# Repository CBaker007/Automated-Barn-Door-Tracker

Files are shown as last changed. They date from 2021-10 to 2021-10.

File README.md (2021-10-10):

# Automated-Barn-Door-Tracker

Astrophotography typically starts with a mount or tracker that can counteract the Earth's rotation to allow long exposure photography. The price for an entry level, commercial tracker capable of holding a DSLR camera can be $350+ USD. DIY trackers (typically called Barn Door Trackers) made of two pieces of wood, a bolt, and hand power to rotate a nut to drive the tracker have been developed. Nico Carver (YouTube Nebula Photos) has such a device with plans and how-to use it here: https://www.youtube.com/watch?v=P_qqLA0WKJg.

The goal of this project is to create a DIY Barn Door Tracker based on Nico's general design and power it with an inexpensive set of electronics (microcontroller, stepper motor, and a motor controller). Additionally, use WiFi to help control the device via a web browser. The end goal would be to create reliable, wide-field DIY Automated Barn Door Tracker for under $50 USD.

Current / near future plans are:
1) Utilize dual core microprocessors to off-load all tracking functions to a dedicated core.
2) Allow for customization and user-defined settings for fine tuning the tracking rates, WiFi settings, and UI. 
3) Use an inexpensive accelerometer to further refine the speed of the motor to more precisely match the Earth's rotation (closed loop system).
4) Slightly modify the design to create a table-top version that does not require a tripod.
5) Utilize an inexpensive ESP32 camera to aid in polar alignment.

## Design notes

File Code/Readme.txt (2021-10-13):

Automated Barn Door Tracker - Compling Code Readme.txt

By default, to program an Ardunio microprocessor, you must flashed with code onto it.  Typically, to
flash the code you must either:
    A) Have the code complied by a compiler (Arduino IDE in our case) and then immediately flashed 
       onto the microprocessor by the same compiler, or 
    B) Have special code placed on the microprocessor that allows pre-compiled code to be downloaded 
       and flashed directly onto it. (Flashing pre-complied code on a blank microprocessor without
       this special code already on it, is possible but it takes a bit of effort.

This project has code built into all versions that allows this direct flashing of pre-compiled code,
called "Over the Air" (OTA) flashing via WiFi.  So once you get the first copy flashed onto the 
microprocessor, you don't have to complie and flash future versions.  Instead you can download new
pre-compiled versions from here and flash it directly from the Automated Barn Door Tracker (ABDT) 
webpage on the microprocessor.

But your new microprocessor must have an initial version of the ABDT code flashed onto it and that still
requires compiling / flashing using the Arduino IDE.

In order to compile and flash the ABDT code in the Arduino IDE, please note the following before proceeding:
    1) These directions were written based on compiling under Windows 10 using Arduino IDE (ver 1.8.15)
       running on an ExpressIF ESP32 microprocessor with WiFi capabilities.  See the code and Parts List
       for exact processor specifications.
       Newer versions and on other platforms may be possible.
    2) Download the Arduino IDE from https://www.arduino.cc/en/software and follow the installation guide
       (Windows: https://www.arduino.cc/en/Guide/Windows)
    3) In order to compile ESP32 code, you must download and install the ExpressIF board definitions.  See the
       guide below for downloading and install them in Arduino IDE.  Just follow the directions for installing from
       Board Manager and no need to follow any OS specific directions:
       https://docs.espressif.com/projects/arduino-esp32/en/latest/installing.html#before-installing
    4) You need to install the stepper library we use.  In Arduino IDE choose Sketch/Include Library/Manage 
       Libraries/Filter for "AccelStepper" and install the latest version.
    5) The sketch uses Over the Air Updates (OTA), AKA - Updating the code via WiFi.  In particular, we are
       using the AsyncElegantOTA running an AsyncWebServer for better webpage handling. These functions
       requires several prerequisite libraries be installed for the code to compile.
       a) In Arduino IDE choose Sketch/Include Library/Manage Libraries/Filter for "AsyncElegantOTA" and install 
          the latest version.
       b) Download and add these two libraries: Download the zip file (look for Code/Download ZIP) from the 
          links below. Save each ZIP file to your computer (one for each link). Then in Arduino IDE under 
          Sketch, Include Library, Add .ZIP Libary and add each one:
          ^ ESPAsyncWebServer.h: https://github.com/me-no-dev/ESPAsyncWebServer
          ^ AsyncElegantOTA.h: https://github.com/me-no-dev/AsyncTCP
     6) You must change the microprocessor we are using in the board definitions.
        In the Arduino IDE, under Tool, Board, select "NodeMCU-32S" (under ExpressIF) if using the recommended
        microprocessor from the parts list.

When you download the Automated Barn Door Tracker code, open it in Arduino IDE and it should compile.

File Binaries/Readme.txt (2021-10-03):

Readme.txt

NEVER CONNECT THE USB TO THE MICROPROCESSOR/DEV BOARD WHILE IT IS CONNECTED TO THE STEPPER MOTOR OR THE BATTERY!!!
NOT RESPONSIBLE FOR ANY DAMAGE TO YOUR USB PORT OR THE MP!!!!

This is the pre-compiled binary for the ESP32 micropocessor and pinouts as described in the sketch:

- Board Info
     + Written for the ESPRESSIF ESP32.
     + Get microprocessor / board definitions for setting up in Arduino IDE from 
       https://docs.espressif.com/projects/arduino-esp32/en/latest/installing.html#before-installing
     + ESP32-WROOM-32D Specs (Specific board datasheet for the board developed on): http://www.hiletgo.com/ProductDetail/1906566.html)
         ^ WiFi = 802.11 b/g/n; BR/EDR + Bluetooth LE v4.2
         ^ 32 GPIO; Op Temp: -40C to 85C;
         ^ 4 MB Flash; 520KB SRAM; 448KB ROM; 0KB PSRAM; 240 MHz
         ^ MP Datasheet: https://www.espressif.com/sites/default/files/documentation/esp32-wroom-32d_esp32-wroom-32u_datasheet_en.pdf
      + There are several specific Expressif ESP32 MP Chips (like ESP32-WROOM-32D) but a whole slew of development boards
        all with different pinouts and voltages.  It is very important that you adjust your particular wiring to reflect this,
        as well as setting the pin references in this file below.  The voltage of this board supports 5.0v (not 3.3v) so the battery
        battery can power the MP and Stepper Motor without a voltage regulator.  Recommended to stick with a 5.0v board where possible 
        to avoid power issues.
      + This may run on future releases for the ESP32-WROOM-32 chip (E, F, etc.) but if you have issues, should re-compile a version
        specific for your version of the chip.
        
      + This is the specific board this binary was developed and tested on though other boards with the same specs should work:
        https://www.amazon.com/gp/product/B0718T232Z/
         - HiLetgo ESP-WROOM-32 ESP32 ESP-32S Development Board 
         - 2.4GHz Dual-Mode WiFi + Bluetooth 
         - Dual Cores Microcontroller Processor 
         - Integrated with Antenna RF AMP Filter AP STA
         - For Arduino IDE

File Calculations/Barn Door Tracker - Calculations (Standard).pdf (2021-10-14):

## Barn Door Tracker – RPM Calculation (using 1/4”-20 bolt)

### 1) Earth’s Rotation

The earth takes 23 hr., 56 min, 4.09053 seconds to rotate 1 revolution or 360 degrees. We will do our calculation for how fast the tracker must move in degrees per minute (dpm) so we will convert the dpm.
Earth DPM = 360 degrees / 23 hr., 56 min, 4.09053 sec
Earth DPM = 360 degrees / (23 hr. * 60 min/hr.) + (56 min) + (4.09053 sec * 1 min/60 sec)
Earth DPM = 360 degrees / 1,380 min + 56 min + 0.0681755 min
Earth DPM = 360 degrees / 1,436.069 min
Earth DPM = 0.25068 degrees/min

### 2) Barn Door Tracker as Right Triangle

Using trigonometry, we can approximate the barn door tracker as a right triangle with a base (bottom of tracker from the center of the hinge to the center of the drive bolt), the top board (hypotenuse), and the drive bolt at a right angle to base. We know that for a 1/4”-20 bolt, it means that the bolt has 20 threads per inch. For ease of use, let’s assume we want to calculate things based on moving the bolt about 1 revolution per minute. Therefore, we can setup our right triangle values we know (in red) with the angle α = 0.25068 degrees/min x 20 min = 5.01369°. We can set the opposite side as 1” (1 inch/20 rev. * 20 rev.).

1"
(at 20 min)

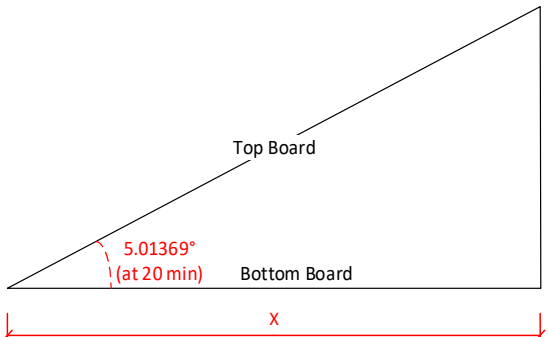
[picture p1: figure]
Top Board; Bottom Board; 5.01369° (at 20 min)

### 3) Calculate Drive Bolt Location

Using trigonometry, we can calculate the distance from the hinge to our drive bolt using: Tan(α) = Opposite/Adjacent
Adjacent * Tan(α) = Opposite
Adjacent = Opposite / Tan(α)
X = 1” / 0.087729
X = 11.40” (or 290 mm)
4) Therefore, if we place the 1/4”-20 drive bolt at 11.40” from the center of the pivot hinge, we can rotate the bolt at 1 revolution per minute to match the Earth’s rotation.
5) It is very important to understand this is an approximation. The right triangle is just an approximation for the angular movement of the Earth’s rotation. As the triangle grows (longer we turn the bolt) the more it will be off. There is very little error for runs of 20 to 25 minutes.

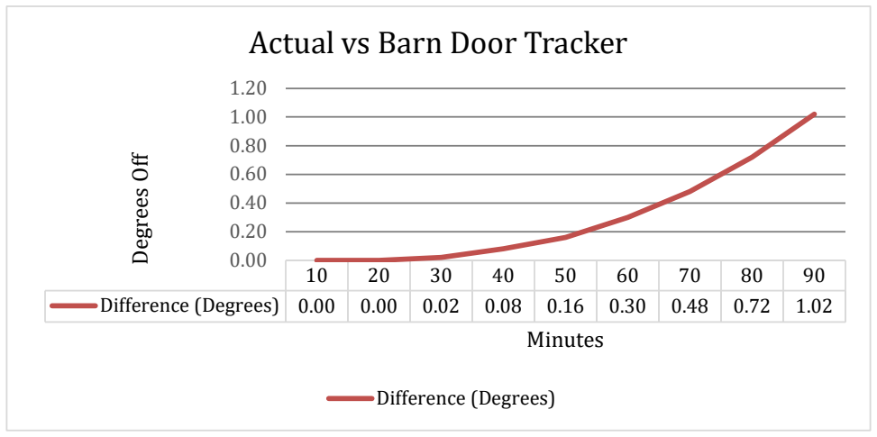
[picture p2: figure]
Difference (Degrees); 1.20 Degrees Off; Minutes; Actual vs Barn Door Tracker

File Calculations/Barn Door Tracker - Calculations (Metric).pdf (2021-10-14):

## Barn Door Tracker – RPM Calculation (using M6‐1 bolt)

1) Earth’s Rotation
The earth takes 23 hr., 56 min, 4.09053 seconds to rotate 1 revolution or 360 degrees. We will do our calculation for how fast the tracker must move in degrees per minute (dpm) so we will convert the dpm.
Earth DPM = 360 degrees / 23 hr., 56 min, 4.09053 sec
Earth DPM = 360 degrees / (23 hr. * 60 min/hr.) + (56 min) + (4.09053 sec * 1 min/60 sec)
Earth DPM = 360 degrees / 1,380 min + 56 min + 0.0681755 min
Earth DPM = 360 degrees / 1,436.069 min
Earth DPM = 0.25068 degrees/min
2) Barn Door Tracker as Right Triangle
Using trigonometry, we can approximate the barn door tracker as a right triangle with a base (bottom of tracker from the center of the hinge to the center of the drive bolt), the top board (hypotenuse), and the drive bolt at a right angle to base. We know that for a M6‐1 bolt, it means that the bolt has 1 thread per mm. For ease of use, let’s assume we want to calculate things based on moving the bolt about 1 revolution per minute. Therefore, we can setup our right triangle values we know (in red) with the angle α = 0.25068 degrees/min x 20 min = 5.01369°. We can set the opposite side as 2 cm (1 cm/10 rev. * 20 rev.).
3) Calculate Drive Bolt Location

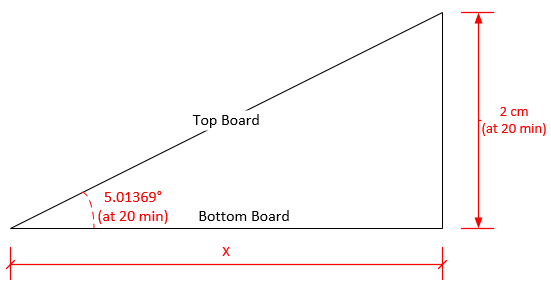
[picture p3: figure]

Using trigonometry, we can calculate the distance from the hinge to our drive bolt using: Tan(α) = Opposite/Adjacent
Adjacent * Tan(α) = Opposite
Adjacent = Opposite / Tan(α)
X = 2 cm / 0.087729
X = 23 cm (or 230 mm)
4) Therefore, if we place the M6‐1 drive bolt at 230 mm from the center of the pivot hinge, we can rotate the bolt at 1 revolution per minute to match the Earth’s rotation.
5) It is very important to understand this is an approximation. The right triangle is just an approximation for the angular movement of the Earth’s rotation. As the triangle grows (longer we turn the bolt) the more it will be off. There is very little error for runs of 20 to 25 minutes.

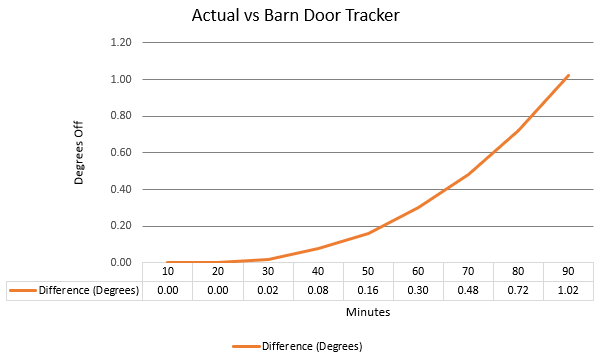
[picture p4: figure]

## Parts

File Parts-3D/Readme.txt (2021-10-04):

This directory contains the current 3D printer files (in .stl format) to create the gears and associated brackets for the barn door tracker.

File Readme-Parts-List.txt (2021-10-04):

Here are list of parts used to build the prototype.   Every part must meet certain specs and substitutes 
will work as long as they meet those specs.  Some parts are more specific (for example the microprocessor)
and while substitutes will work, you must verify every spec or possibly re-write/change the code and recompile
a new binary.

Initial build based on Nico Carver's Barn Door Tracker:
  * Video Here: https://www.youtube.com/watch?v=P_qqLA0WKJg 
  * Build Document Here (as of 2021): https://drive.google.com/file/d/1xJgKvlnahubcNM2y2DRTjEfHE8nX8fVD/view
  * Nico based his on the 'Sky and Telescope' magazine article in the April 1975 by George Haig of Glasgow, Scotland.
  * Since he was from Scotland, it is sometimes referred to as the Scotch Mount.  
  * More recently commonly referred to as a Barn Door Tracker.

/////////////
/// NOTES ///
/////////////
1) These parts listed are not necessarily the cheapest place to obtain them.   It was decided to show the parts
   for the most common, easiest to get locations in the US, rather than numerous, smaller speciality stores.
   We tried to list quality parts and the number required.   In some cases, you need to buy more than are required
   because the minimum order is larger.  Other stores may sell for less in smaller quantities.
2) It may be possible to find these exact parts or others similar, in exact quantities, from other places like AliExpress,
   eBay, Arduino Speciality stores, etc.  Just make sure the requirements for any alternative parts are the same.
3) In the end, the savings may only be minimal. 
4) Might be able to save money by sharing  the costs with someone and building 2 or more.

///////////////////
/// Assumptions ///
///////////////////
  * Have access to a 3D printer to make the required gears.
  * Have AA Batteries x4
  * Have a sturdy tripod to mount the Barn Door Tracker on.
  * Have a ball head for your camera.
    One option if you don't have one:
    https://www.ebay.com/itm/360-Degree-Mini-Tripod-Ball-Head-Ball-head-Compass-with-Quick-release-Plate-BK03-/112014868235
  * Have a camera and wide-field lens (DSLR and sub 100mm FL lens or a cell phone with long exposure capabilites)
  * Have some basic tools:
    - Saw to cut wood.
    - Measuring tape or ruler
    - Drill with some various drill bits
    - Screw drivers
    - Hammer (may not be needed)
    - Pliers (useful but not required)

////////////
// Amazon //
////////////
=== Please use this affiliate link so Nico Carver gets a small reward from Amazon - doesn't cost you anything! ===
=== Helps support Nico's work and make projects like this possible. Just click on link and then shop / checkout. ===
=== https://amzn.to/31rYb56 ===
* Microprocessor
  HiLetgo ESP-WROOM-32 ESP32 ESP-32S Development Board 2.4GHz Dual-Mode WiFi + Bluetooth Dual Cores
  (Specifically: ESP32, ESP-WROOM-32D chip, WiFi, Dual-Core, 5.0V / not 3.3v, Pre-Solder Pins, Specific pinouts)
  https://www.amazon.com/gp/product/B0718T232Z/
* Stepper Motor with Motor Controller
  You only need a single motor and controller, but it is typically the same price or cheaper to buy a 5 pcs set vs 1
  Additionally, some versions are not as reliable as others.  Elegoo has a good rating.
  28BYJ-48 ULN2003 5V Stepper Motor + ULN2003 Driver Board - 5 sets
  https://www.amazon.com/ELEGOO-28BYJ-48-ULN2003-Stepper-Arduino/dp/B01CP18J4A
* Breadboard and Jumpers Kit (not needed if you can solder and have small guage wire)
  Paxcoo 4 Pieces Breadboards Kit with 120 Pieces Jumper Wires
  https://www.amazon.com/Paxcoo-Breadboards-Arduino-Circboard-Prototyping/dp/B0727X6N9D/
* Battery Holder (with snap connector)
  Only need 1 but snap connector nice feature.  You can get a single with wire or if you can solder, without wires
  4 x 1.5V (6V) AA Battery Holder with 9V Type Snap Connector - 3+3 Pcs
  https://www.amazon.com/Battery-Holder-Connector-Plastic-Housing/dp/B07F43VWRQ/

///////////
// Lowes //
///////////
[NOTE: Or Menards if you have those near you ... NOTE: Home Depot doesn't tend to carry some full length threaded bolts.]

* Drive Bolt - x1 (must be: 1/4-20, Hex Head, Full Thread, and at least 3" long but 5-in better.)
  [NOTE: These are sometimes called Hex Head Tap Bolts.]
  Hillman 1/4-in x 5-in Zinc-Plated Coarse Thread Hex Bolt (2-Count) (Item #214117, Model #883150)
* Drive Nut for Large Gear - x1 (must be 1/4-20 hex)
  https://www.lowes.com/pd/Hillman-1-4-in-x-20-Zinc-Plated-Steel-Hex-Nut/3058547
* Tripod Nut - x1 (Most tripods have a 1/4-20 bolt.  Some might use a 3/8-16.  Verify with yours.)
  [Could buy adapter to use both: https://www.amazon.com/Standard-Adapter-Converter-Camcorder-Ballhead/dp/B07567PHSZ/]
  https://www.lowes.com/pd/Hillman-2-Count-1-4-in-Zinc-Plated-Standard-SAE-3-Prong-Tee-Nuts/3012529
* Hinge (Two Options)
  [Option 1: Buy two 2-inch hinges and mount one on top edge and one on bottom edge.  Must take time to align even with side.]
  https://www.lowes.com/pd/Gatehouse-2-in-Zinc-Mortise-Door-Hinge-2-Pack/50041810
  [Option 2: Buy a single piano hinge and use a hacksaw to cut it to length.  Made to be cut, but need saw to cut it.]
  https://www.lowes.com/pd/Gatehouse-Nickel-Piano-Cabinet-Hinge/1000486043
* Machine Screws for Motor x2 (need screw and nut)
  #6-32 Machine Screw x 1/2"
  https://www.lowes.com/pd/Hillman-6-32-x-1-2-in-Phillips-Drive-Machine-Screws-12-Count/3815411
* Machine Screws for Gear Bracket x4
  #6-32 Machine Screw x 1-1/2"
  https://www.lowes.com/pd/Hillman-6-32-x-1-1-2-in-Phillips-Drive-Machine-Screws-10-Count/3816093
* Machine Screws - #6 Lock Washers - x6 (x2 Motor and x4 Gear Bracket)
  https://www.lowes.com/pd/Hillman-4-Count-6-Standard-SAE-Split-Lock-Washer/999996210
* Barn Door Wood x2 (top and bottom)
  1x6 Pine Board - 6' long
  https://www.lowes.com/pd/Top-Choice-Common-1-in-x-6-in-x-6-ft-Actual-0-75-in-x-5-5-in-x-6-ft-Pine-Board/1000894238

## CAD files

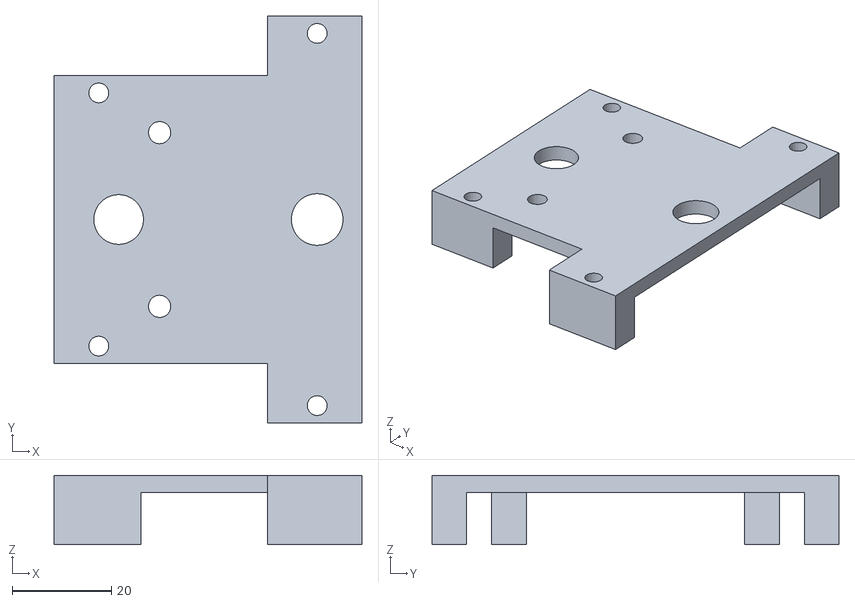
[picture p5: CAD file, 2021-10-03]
Parts-3D/Barn Door Tracker - Stepper Motor Gears - Part 1 - v1.6.stl
62.0 x 82.0 x 14.0

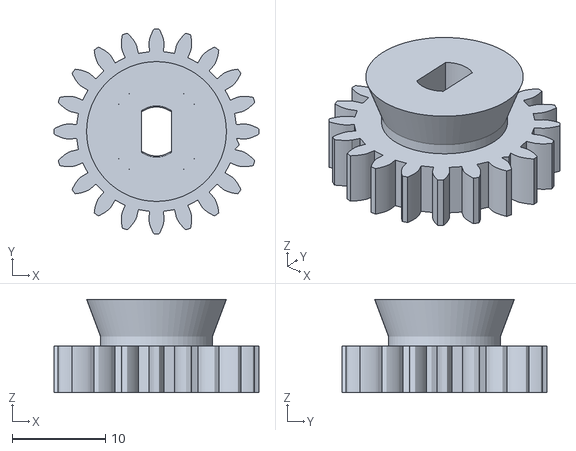
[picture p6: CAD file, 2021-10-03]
Parts-3D/Barn Door Tracker - Stepper Motor Gears - Part 2 - v1.7.stl
22.0 x 22.0 x 10.0

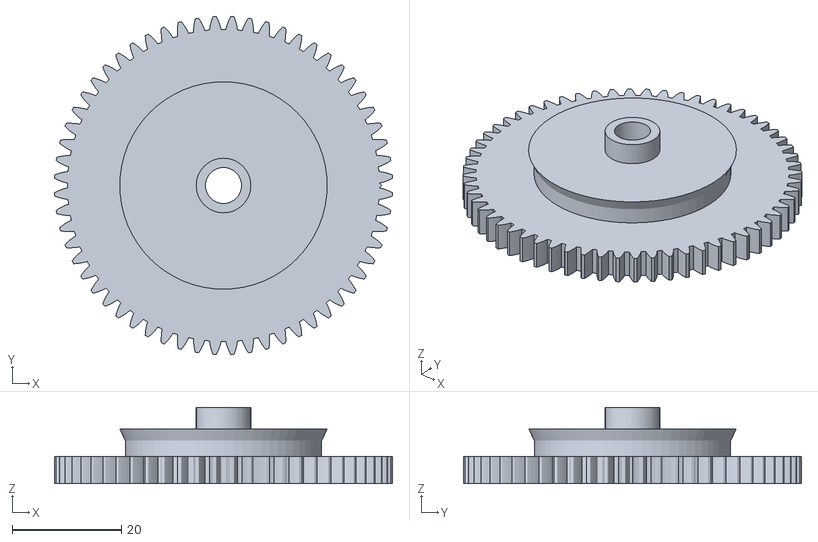
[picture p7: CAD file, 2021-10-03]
Parts-3D/Barn Door Tracker - Stepper Motor Gears - Part 3 - v1.6.stl
61.9 x 61.9 x 14.0

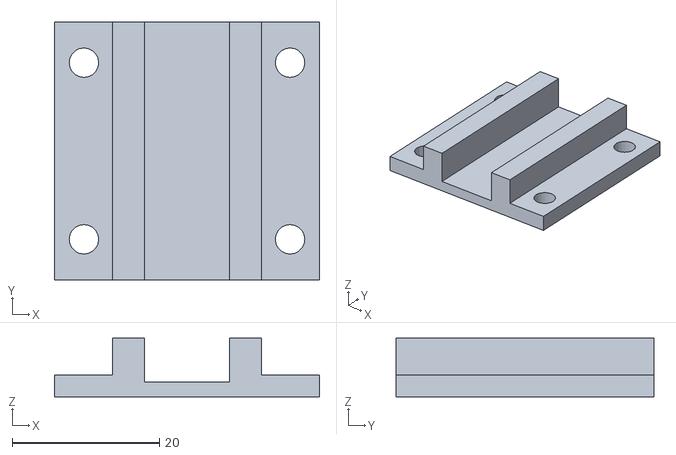
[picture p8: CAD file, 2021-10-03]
Parts-3D/Barn Door Tracker - Stepper Motor Gears - Part 4 - v1.2.stl
36.0 x 35.0 x 8.00

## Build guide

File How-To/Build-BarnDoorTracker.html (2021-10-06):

# Base Unit - Wood Parts

## Step 1 - Cut 1x6" Pieces

1. Cut two pieces of the 1x6 boards to 12-3/4" (12.75" or 324mm) long.
2. Mark one board "Top" and one "Bottom".

## Step 2 - Attach Hinge(s)

1. The parts list suggests two different options for the hinge; A single piano hinge or Two 2" (50 mm) long hinges.
2. If you are using a single piano hinge, first cut it to be slightly narrower than the 1x6 board's width (5-1/4" or 133 mm).
3. Measure the width of your hinge (not including the round, pivot part).
4. Draw a line, that distance and parallel from the short edge, one on the left edge of the "Bottom" board and one on the right edge of the "Top" board. This line helps keep the hinges parallel to the edge and keeps the boards aligned when closed.
5. Using the lines, mount the hinge(s) so it is parallel to the edge, following the line.

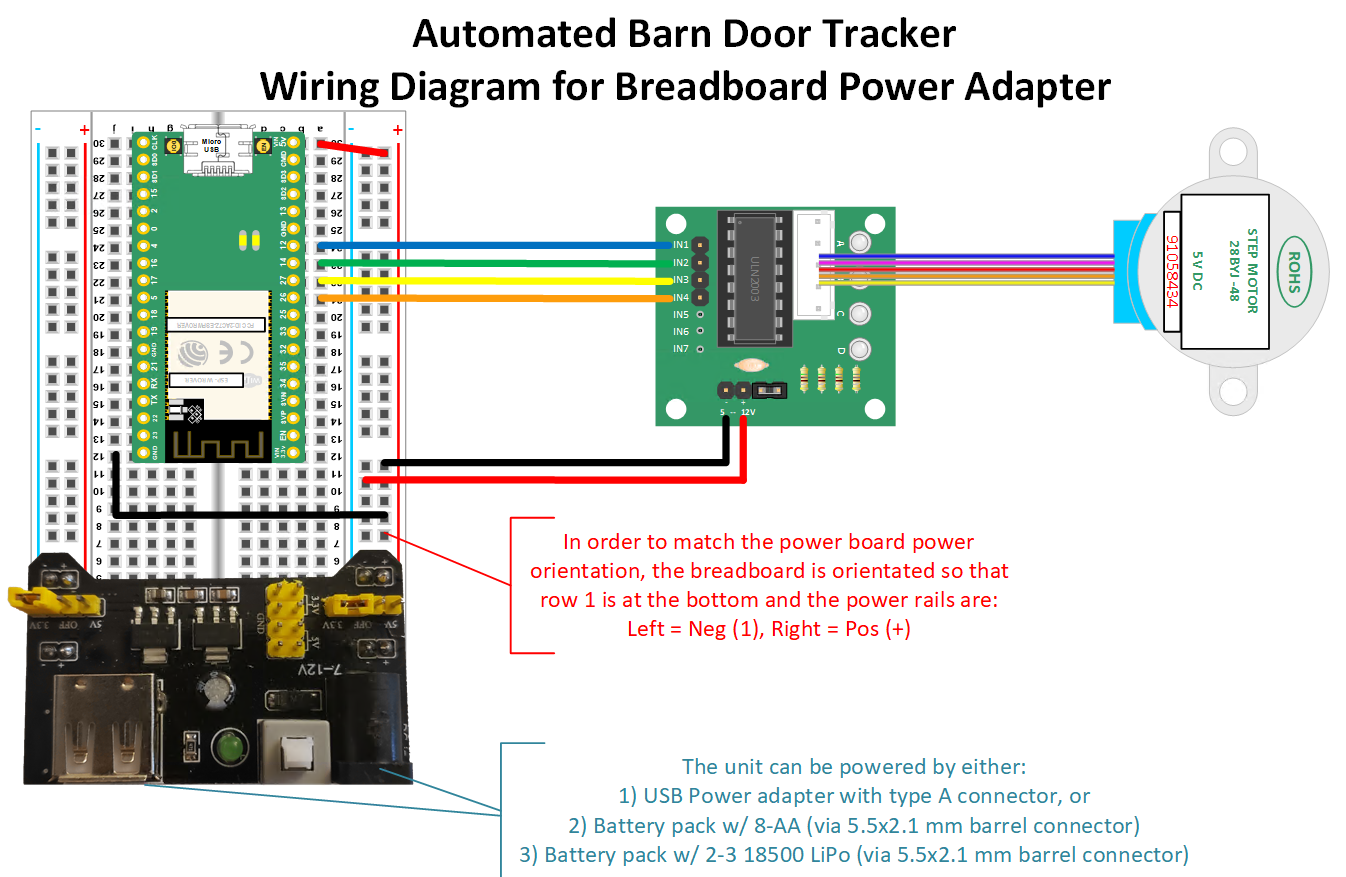
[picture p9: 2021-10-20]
How-To/AutomatedBarnDoor-WiringDiag-USBPowerAdptr.png

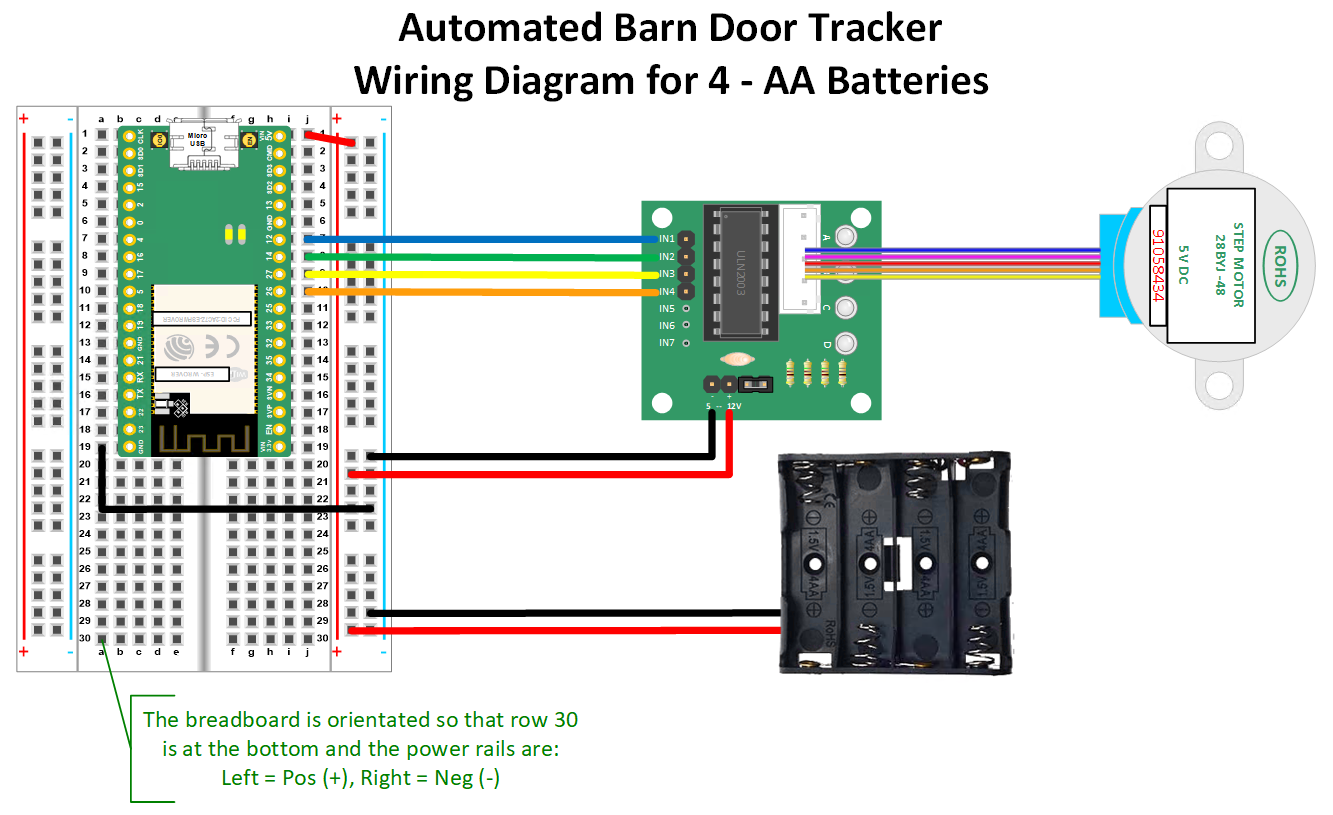
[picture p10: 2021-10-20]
How-To/AutomatedBarnDor-WiringDiag-4AABatteries.png

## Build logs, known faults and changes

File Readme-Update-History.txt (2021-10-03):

2021-10-03 - v1.3d (Web GUI version 00.03.A) - Initial Release
===============================================================
    // FEATURES //
    * Sideral rate hard coded to 106.  (Future upgrade to allow this to be tuned and changed / saved from Web GUI.)
    * OTA Updates enabled.
    * WiFi has the following fixed settings:
      - AP mode only.
      - IP is 192.168.4.1
      - SSID is "BarnDoorTracker" and password = "NebulaPhotos" are hard coded.
      - (Future upgrade may be to allow these to be updated/changed from Web GUI.)

    // KNOWN ISSUES //
    * Set release version to match Web GUI Ver.

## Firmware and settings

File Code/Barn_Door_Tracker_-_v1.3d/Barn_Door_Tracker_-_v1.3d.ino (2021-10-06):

/*
Runs a single 28BYJ-48 stepper motors with AccelStepper Library.
NOTES:
 - Stepper Motor
     + Using the library you must download and install if not in contributed libraries: https://www.arduinolibraries.info/libraries/accel-stepper
     + The 28BYJ-48 draws 240mA per https://lastminuteengineers.com/28byj48-stepper-motor-arduino-tutorial/
     + The microprocessor should be able to support this, but they typically recommend a separate +5V power supply.
     + If we could use the MP power, we could run the whole system from a USB cable.
 - Board Info
     + Written for the ESPRESSIF ESP32.
     + Get microprocessor / board definitions for setting up in Arduino IDE by following 
       https://docs.espressif.com/projects/arduino-esp32/en/latest/installing.html#before-installing
     + ESP32-WROOM-32D Specs (Specific board datasheet for the board developed on): http://www.hiletgo.com/ProductDetail/1906566.html)
         ^ WiFi = 802.11 b/g/n; BR/EDR + Bluetooth LE v4.2
         ^ 32 GPIO; Op Temp: -40C to 85C;
         ^ 4 MB Flash; 520KB SRAM; 448KB ROM; 0KB PSRAM; 240 MHz
         ^ MP Datasheet: https://www.espressif.com/sites/default/files/documentation/esp32-wroom-32d_esp32-wroom-32u_datasheet_en.pdf
      + There are several specific Expressif ESP32 MP Chips (like ESP32-WROOM-32D) but a whole slew of development boards
        all with different pinouts and voltages.  It is very important that your adjust your particular wiring to reflect this,
        as well as setting the pin references in this file below.
 - OTA Updates
      + Running AsyncWebServer for better webpage handling - https://arduino-esp8266.readthedocs.io/en/latest/esp8266wifi/soft-access-point-class.html
      + https://www.arduino.cc/reference/en/libraries/asyncelegantota/
      + Following examples from AsyncElegantOTA to do OTA Updates.
      + Need to add libraries below to use these functions (download zip and install in Arduino IDE Libraries):
          ^ In Arduino IDE choose Sketch/Include Library/Manage Libraries/Filter for "AsyncElegantOTA" and install latest version.
          ^ In Arduino IDE choose Sketch/Include Lib/Add .ZIP Library install the following two downloads:
          ^ ESPAsyncWebServer.h: Download ZIP from https://github.com/me-no-dev/ESPAsyncWebServer
          ^ AsyncElegantOTA.h: Download ZIP from https://github.com/me-no-dev/AsyncTCP
*/

//GLOBAL DEFINITIONS

// Setup the pins between your MP and motor controller
// Must verify for your particular microprocessor board
// These are digital output pins on your mp
// Using HitLetGo ESP32-WROOM-D2 board
#define motor1Pin1  12    //IN1 UNL2003APG - 28BYJ48 pin 1
#define motor1Pin2  14    //IN2 UNL2003APG - 28BYJ48 pin 2
#define motor1Pin3  27    //IN3 UNL2003APG - 28BYJ48 pin 3
#define motor1Pin4  26    //IN4 UNL2003APG - 28BYJ48 pin 4
                          //Battery 5V     - 28BYJ48 (VCC)
                          //Battery GND    - 28BYJ48 (GND) 

// Must set the max speed of your stepper motor.
// This varies depending on battery, MP, stepper controller, and stepper motor
// If set to high, the lights on the motor controller will flash but the stepper will not move.
// In that case, lower until it starts moving.
// Good starting number is around 500 - 600.  Most low end systems won't get too much higher.
int STEPMAXSPEED = 600;

// Must calculate for your setup.  If using the same parts, should be very close.  
// In our setup, we want 1 revolution of output (3 input revs = 1 output rev) in 1 minute
// Should test before using to make sure correct for your setup.
// NOTE: Don't do any other functions on MP while running it.  Web browser access, LED on/off, etc all affect CPU load and hence RPM
long STEPSIDREAL = 102;   // Inital testing suggest 102 in our setup with a power supply.  How does battery affectd this?


// Global Variables

// Set Initial Stepper Motion
// Typically set to CCW/Up/Run in case user does not have or want to connect to webpage
char chrStepMotion = 'U';  // 'U'=Up/CCW/Run, 'D'=Down/CW, 'S'=Stop

// My IP for WiFi when acting as AP
// No need to change unless a conflict
IPAddress myIP(192,168,4,1); 
IPAddress myGATEWAY(192,168,4,255);
IPAddress mySUBNET(255,255,255,0);
char myHOSTNAME[7+1] = "tracker";  //  Using ESPmDNS to set a local DNS name of http://tracker.local so access via hostname or IP


/////////////////////////////////////////
// Should not have to change below here
/////////////////////////////////////////

// Software Version
char chrSOFTWAREVER[8] = "00.03.A";

// Running gear ratio of 3:1 so output is 3x this number
// Full rotation on stepper is 2038 per specs
// Some motors are not the same spec, so it may be different for a particular motor.  Not using this ATM.
#define FULLRotation 2038

// Stepper can be setup as full or half steps
#define FULLSTEP 4
#define HALFSTEP 8

// NOTE: The sequence 1-3-2-4 is required for proper sequencing of 28BYJ48
// Run in half steps
#include <AccelStepper.h>
AccelStepper stepper1(FULLSTEP, motor1Pin1, motor1Pin3, motor1Pin2, motor1Pin4);


/*
  Parts of WiFi Code....
  Developed from Sample for ExpressIF Docs (https://docs.espressif.com/projects/arduino-esp32/en/latest/api/wifi.html#ap-example)

  WiFiAccessPoint.ino creates a WiFi access point and provides a web server on it.
  Steps:
  1. Connect to the access point "yourAp"
  2. Point your web browser to http://192.168.4.1/H to turn the LED on or http://192.168.4.1/L to turn it off
     OR
     Run raw TCP "GET /H" and "GET /L" on PuTTY terminal with 192.168.4.1 as IP address and 80 as port

  Created for arduino-esp32 on 04 July, 2018
  by Elochukwu Ifediora (fedy0)
*/

#include <WiFi.h>
#include <WiFiClient.h>
#include <WiFiAP.h>
#include <ESPmDNS.h>
#include <AsyncTCP.h>   // Added for AsyncElegantOTA
#include <ESPAsyncWebServer.h>  // Added for AsyncElegantOTA - Download ZIP of code + add to IDE Libraries: https://github.com/me-no-dev/ESPAsyncWebServer
#include <AsyncElegantOTA.h>  // Added for AsyncElegantOTA - Download ZIP of code + add to IDE Libraries: https://github.com/me-no-dev/AsyncTCP


// Set the GPIO pin where you connected your test LED or comment this line out if your dev board has a built-in LED
// My dev board has built in, not needed
// #define LED_BUILTIN 2   

// Set these to your desired credentials.
const char *ssid = "BarnDoorTracker";
const char *password = "NebulaPhotos";

// Setup Servers
AsyncWebServer server(80);

// Main Loop Counter
unsigned long ulongMainLoopCounter = 0;

void setup()
{
  // Debug Output to Serial
  Serial.begin(115200);
  Serial.println();
  Serial.println("Booting (Setup)...");

  
  // For Debugging - Flash Built-In LED during each loop
  // Initialize digital pin LED_BUILTIN as an output for using built-in LED
  pinMode(LED_BUILTIN, OUTPUT);

  //
  // Setup the Stepper Motor
  //
  stepper1.setMaxSpeed(STEPMAXSPEED);     // If set to high, motor will not move
  // stepper1.setAcceleration(50.0);      // Don't set this, we are using constant speed.
  stepper1.setSpeed(-STEPSIDREAL);        // We require neg number for CCW rotation (tracker moves up)
  // stepper1.moveTo(2038);               // For Debugging Only - 1 revolution CW is 2038 steps (neg for CCW) - Some disagreement about this.  Must test

  //
  // Setup the WiFi
  // (already setup above)
  // More info on ESP8266 Soft AP at https://arduino-esp8266.readthedocs.io/en/latest/esp8266wifi/soft-access-point-class.html
  
  // Debug Output to Serial
  Serial.println("Configuring WiFi in Soft AP Mode ...");

  // Set the WiFi in Soft AP Mode for the ESP8266
  WiFi.mode(WIFI_AP);
  // Set IP, Subnet, GW
  if (WiFi.softAPConfig(myIP, myGATEWAY, mySUBNET) == false) {
    Serial.println("Setting IP, Subnet, and Gateway failed.");
  }
  // If you remove the password parameter, their will not be a preshared key (WPA2-PSK) and the AP will be "open".  
  // We have a password-psk to secure it for star parties and group sessions.
  // Start WiFi in AP mode.
  WiFi.softAP(ssid, password);
  myIP = WiFi.softAPIP();
  Serial.print("AP IP address: ");
  Serial.println(myIP);

  //Setup Server Webpages
  server.on("/test", HTTP_GET, [](AsyncWebServerRequest *request){
    request->send(200, "text/plain", "message received");
  });

  server.on("/LON", HTTP_GET, [](AsyncWebServerRequest *request){
    digitalWrite(LED_BUILTIN, HIGH);                 // GET /H turns the LED on
    Serial.println("LED set to High (on).");         // Debug to serial output
    request->redirect("/");                          // back to homepage
  });

  server.on("/LOFF", HTTP_GET, [](AsyncWebServerRequest *request){
    digitalWrite(LED_BUILTIN, LOW);                  // GET /L turns the LED off
    Serial.println("LED set to Low (off).");         // Debug to serial output
    request->redirect("/");                          // back to homepage
  });

  server.on("/RUN", HTTP_GET, [](AsyncWebServerRequest *request){
    chrStepMotion = 'U';                             // turn stepper to move up / run
    request->redirect("/");                          // back to homepage
  });

  server.on("/DOWN", HTTP_GET, [](AsyncWebServerRequest *request){
    // turn stepper to move down / reset  (BE CAREFUL NO SENSOR TO STOP WHEN ALL THE WAY DOWN - DON'T BURN MOTOR
    chrStepMotion = 'D';                             // turn stepper to move down / reset  
                                                     // (BE CAREFUL NO SENSOR TO STOP WHEN ALL THE WAY DOWN - DON'T BURN MOTOR
    request->redirect("/");                          // back to homepage
  });

  server.on("/STOP", HTTP_GET, [](AsyncWebServerRequest *request){
    chrStepMotion = 'S';                             // stop stepper
    request->redirect("/");                          // back to homepage
  });

  server.on("/", HTTP_GET, [](AsyncWebServerRequest *request){
    AsyncResponseStream *response = request->beginResponseStream("text/html");
    // set header and body
    response->addHeader("Server","Nebula Photos Barndoor Tracker");
    response->print("<!DOCTYPE html><html>");  
    response->print("<html><head>");
    response->print("<style>");
    response->print("body {background-color: black;}");
    response->print("h1 {color: white; font-size: 50px;}");
    response->print("h5 {color: white; font-size: 30px;}");
    response->print("p {color: white; font-size: 40px;}");
    response->print("a, a:link, a:visited {color:red;}");
    response->print(".f50 {color: white; font-size: 50px;}");
    response->print(".f30 {color: white; font-size: 30px;}");
    response->print(".mytable1{border-collapse:collapse;border-spacing:0;width:100%;table-layout:fixed;display:table}");
    response->print(".mytable1 tr{border-bottom:1px solid #ddd}");
    response->print(".mytable1{border:1px solid black}");
    response->print(".mytable1 tr:nth-child(odd){background-color:black}");
    response->print(".mytable1 tr:nth-child(even){background-color:black}");
    response->print(".mytable1 td,.mytable1 th{font-size: 20px; color: yellow; padding:8px 8px;display:table-cell;text-align:center;vertical-align:middle}");
    response->print(".mytable1 th:first-child,.mytable1 td:first-child{padding-left:16px}");
    response->print(".mytable2 {width: 100%; border:10px solid black;}");
    response->print(".mytable2 tr {background: #2B289E; border-color: black; border: 15px solid black;}");
    response->print(".mytable2 td, .mytable2 th {font-size: 60px; font-color: white; text-align:center; border: 15px solid black;}");
    response->print(".mytable3{border-collapse:collapse;border-spacing:0;width:100%;table-layout:fixed;display:table}");
    response->print(".mytable3{border:1px solid black}");
    response->print(".mytable3 tr{border-bottom:1px solid #ddd}");
    response->print(".mytable3 td,.mytable1 th{font-size: 16px; color: white; padding:8px 8px;display:table-cell;text-align:center;vertical-align:middle}");
    response->print(".mytable3 td a, .mytable3 td a:link, .mytable3 td a:visited {color:white;}");
    response->print("</style><title>Nebula Photos Barndoor Tracker - Main Page</title></head>");
    response->print("<body><br>");
  
    // page title
    response->print("<center>");
    response->print("<div class='f50'>Nebula Photos Barndoor Tracker<br></div>");
    response->print("</center>");
              
    // the main body
    response->print("<table class='mytable1'><tr>");
    response->print("<td>Max Step Speed: ");
    response->printf("%d",STEPMAXSPEED);
    response->print("</td>");
    response->print("<td>Sidreal Speed: ");
    response->printf("%d",STEPSIDREAL);
    response->print("</td>");
    response->print("<td>Motion State: ");
    response->printf("%c",chrStepMotion);
    response->print("</td>");
    response->print("</tr><tr>");
    response->print("<td>WiFi Mode: ");
    response->print("AP");
    response->print("</td>");
    response->print("<td>WiFi SSID: ");
    response->printf("%s",ssid);
    response->print("</td>");
    response->print("<td>Tracker IP: ");
    response->printf("%u.%u.%u.%u",myIP[0],myIP[1],myIP[2],myIP[3]);
    response->print("</td>");
    response->print("</tr></table>");
              
    // the content of the HTTP response follows the header:
    response->print("<table class='mytable2'>");
    response->print("<tr>");
    response->print("<td><a href=\"/LON\">LED On</a></td>");
    response->print("<td><a href=\"/LOFF\">LED Off</a></td>");
    response->print("</tr>");
    response->print("<tr>");
    response->print("<td><a href=\"/RUN\">RUN (CCW)</a></td>");
    response->print("<td><a href=\"/DOWN\">Down (CW)</a></td>");
    response->print("</tr>");
    response->print("<tr>");
    response->print("<td><a href=\"/STOP\">STOP</a></td>");
    response->print("<td><a href=\"/STOP\">STOP</a></td>");
    response->print("</tr>");
    response->print("</table>");

    // footer
    // copyright, update link, version, etc
    response->print("<table class='mytable3'>");
    response->print("<tr>");
    response->printf("<td align=\"left\">Stations Connected: %d</td>", WiFi.softAPgetStationNum());
    response->printf("<td align=\"center\">%s (<a href=\"/update\">Update Software</a>)</td>", chrSOFTWAREVER);
    response->print("<td align=\"right\">Written By / Copyright: <a href=\"mailto:netspec.inc@gmail.com\">Christopher Baker</a></td>");
    response->print("</tr>");
    response->print("</table>");

    // end header and body
    response->print("</body></html>");
    // send the response
    request->send(response);
  });

  server.on("/SET", HTTP_GET, [](AsyncWebServerRequest *request){
    AsyncResponseStream *response = request->beginResponseStream("text/html");
    //List all parameters
    int params = request->params();
    for(int i=0;i<params;i++){
      AsyncWebParameter* p = request->getParam(i);
//      char *strPName = p->name().c_str();
//      char *strPValue = p->value().c_str();     
      Serial.printf("GET[%s]: %s\n", p->name().c_str(), p->value().c_str());
      response->printf("<center>Parameter Name: %s</center>", p->name().c_str());
      response->printf("<center>Parameter Value: %s</center>", p->value().c_str());

      // Figure out what mode we are in and set speed
      if ( strcmp((p->name().c_str()),"sidreal") ) {
        STEPSIDREAL = p->value().toInt();         // Set new sidreal speed.
        response->printf("<center>Set %s to %i</center>", p->value().c_str(), p->value().toInt());
      }
    }
    request->send(response);
  });

//    if(p->isFile()){ //p->isPost() is also true
//      Serial.printf("FILE[%s]: %s, size: %u\n", p->name().c_str(), p->value().c_str(), p->size());
//      } else if(p->isPost()){
//        Serial.printf("POST[%s]: %s\n", p->name().c_str(), p->value().c_str());
//        } else {
//          Serial.printf("GET[%s]: %s\n", p->name().c_str(), p->value().c_str());
//          }
//    }
//  }

  // Start ElegantOTA for OTA updates via Web - http://<myIP>/update
  AsyncElegantOTA.begin(&server);    // Start ElegantOTA

  // Start the webserver
  server.begin();
  Serial.println("Web Server started");
  
}


void loop()
{

  // Figure out what mode we are in and set speed
  switch (chrStepMotion) {
    case 'U':
      // Move Up Direction / Run - CCW in our setup
      stepper1.setSpeed(-STEPSIDREAL);                         // Set to sidreal speed.
      //Serial.println("Rotate CCW (Run) at Sidreal speed.");  // Debug to serial output
      break;
    case 'D':
      // Move Down Direction - CW in our setup
      stepper1.setSpeed(STEPMAXSPEED);                          // Set to max speed for testing.  Move down.
      //Serial.println("Rotate CW (down) at Max speed.");       // Debug to serial output
      break;
    case 'S':
      // Stop Moving
      stepper1.setSpeed(0);                                     // Set to zero to stop it rotating.
      //Serial.println("Stop all Rotation.");                   // Debug to serial output
      break;
    default:
      // DEFAULT - Move Up Direction / Run - CCW in our setup
      stepper1.setSpeed(-STEPSIDREAL);                          // Set to sidreal speed.
      //Serial.println("DEFAULT TO - CCW (Run) at Sidreal.");   // Debug to serial output
      break;
  }

  // Step/Run stepper motor
  // Ideally move this to its own task / core so these processes don't affect the critical timing of this process.
  stepper1.runSpeed();

  // Check to see if an OTA Update should be initiated
  AsyncElegantOTA.loop();

}
